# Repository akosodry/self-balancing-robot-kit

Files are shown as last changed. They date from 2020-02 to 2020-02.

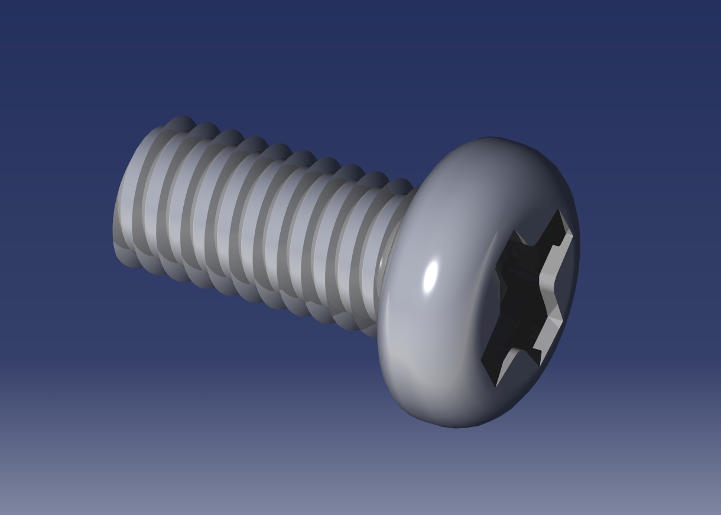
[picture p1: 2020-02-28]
2_Solidworks models (student work)/2_Solidworks models (student work)/m3x10-philips-head-screw-1.snapshot.2/M3x6.jpg

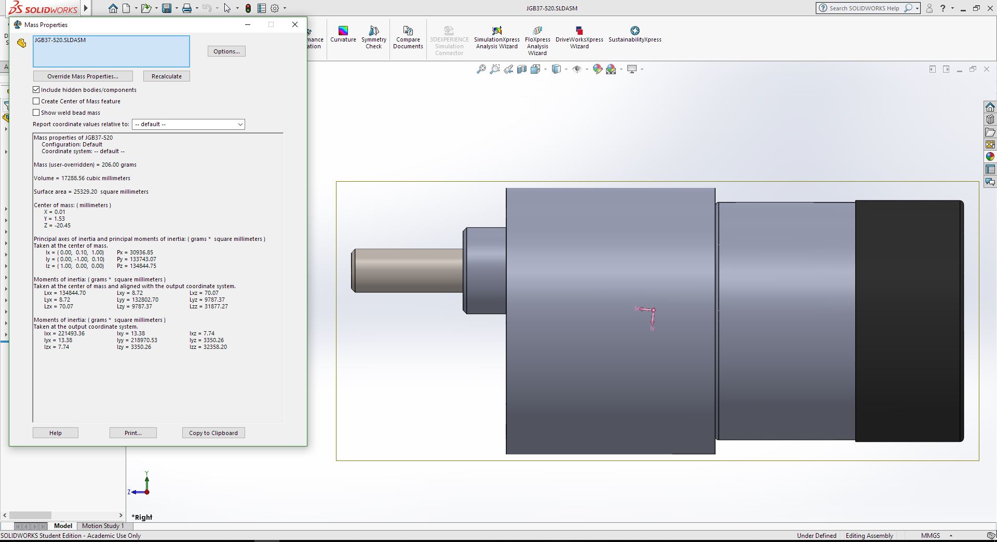
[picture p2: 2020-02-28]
2_Solidworks models (student work)/2_Solidworks models (student work)/Motor/Ellenőrző képek/Oldalnezet.JPG

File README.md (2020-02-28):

# self-balancing-robot-kit
The supplementary online material for the article: FUZZY CONTROL OF SELF‐BALANCING ROBOTS: A CONTROL LABORATORY PROJECT

**Cite this work as:**

Odry Á, Fullér R, Rudas IJ, Odry P. **Fuzzy control of self‐balancing robots: A control laboratory project**. Comput Appl Eng Educ. 2020;1–24. https://doi.org/10.1002/cae.22219

A **short video demonstration** of the closed loop behavior is available **here**:
https://youtu.be/y2i62vh2vE4

The paper systematically describes the construction, development and fuzzy control of the proposed lab setup for teaching control system design in laboratories. All the information, including the STL files for 3D printing, computer-aided design (CAD) models, MATLAB/Simulink files, and MCU software have been made publicly available here to help other lab teams in designing similar experiments.

The description of the files is summarized as follows.

**1_3D printer files** This file contains the STL files that can be used in 3D printing software such as Ultimaker Cura.

**2_Solidworks models** 	This file contains the CAD model of the lab setup. It was created by a mechatronic engineering student at the University of Dunaújváros.

**3_Minimal working environment**	This file contains the Arduino code that initializes the MCU peripherals of the lab setup, drives the motors in both directions, and reads and sends the instantaneous IMU (acceleration and angular rate) and encoder (motor shaft position) measurements to the PC.

**4_MATLAB script to record data**	This file contains the MATLAB code used to collect the measurement results via the serial port. The file also contains the recorded measurement results.

**5_DC motor model**	This file contains both the Simulink model of the DC motor and the Simulink Design Optimization session file.

**6_Robot model open loop**	This file contains the S-function-based Simulink model of the robot.

**7_Robot model closed loop**	This file contains the Simulink model of the fuzzy control strategy.

**8_LUT generation**	This file contains the MATLAB functions that generate the lookup-table approximation of the fuzzy logic controllers.

**9_Arduino closed loop**	This file contains the Arduino code that applies the fuzzy control strategy to stabilize the robot.

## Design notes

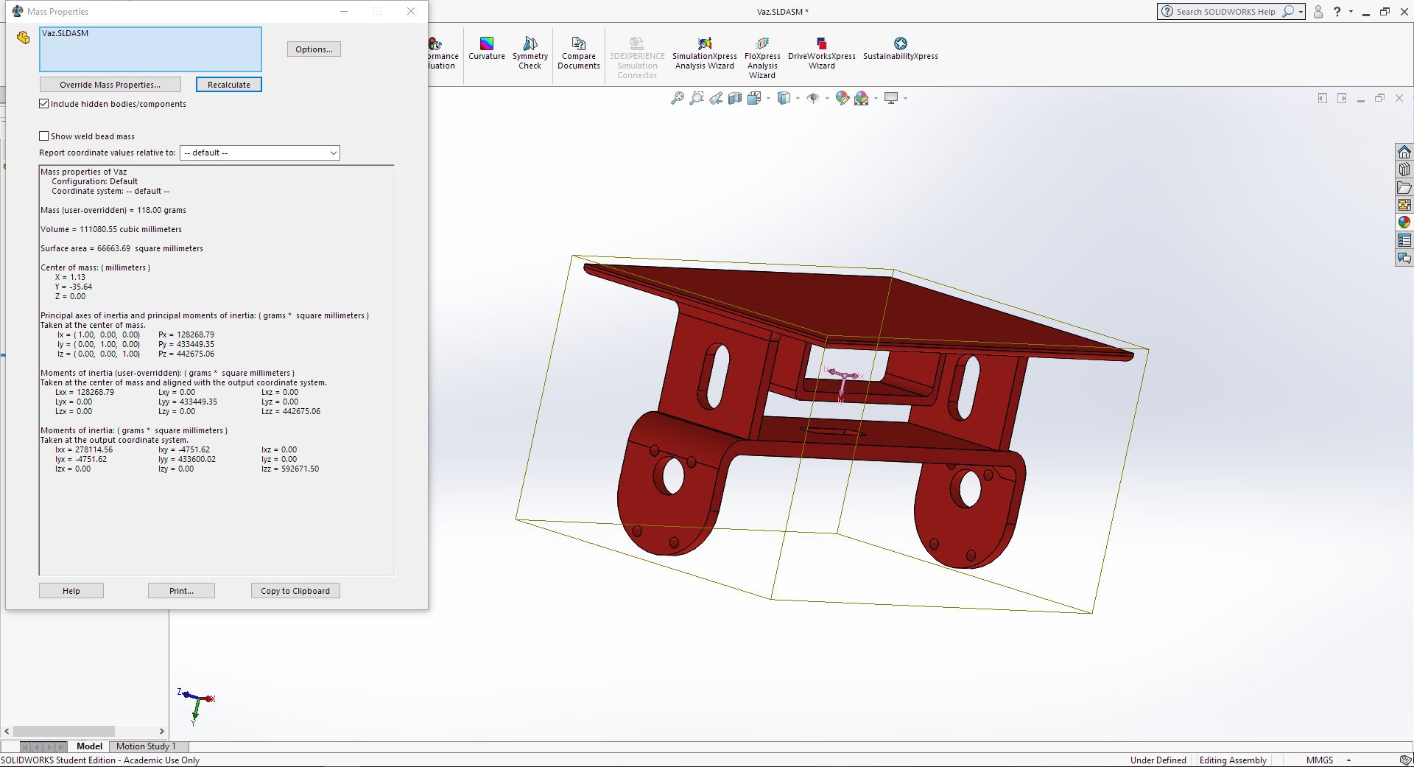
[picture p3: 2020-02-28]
2_Solidworks models (student work)/2_Solidworks models (student work)/Váz/Ellenőrző képek/Vaz_Ellenorzo.JPG

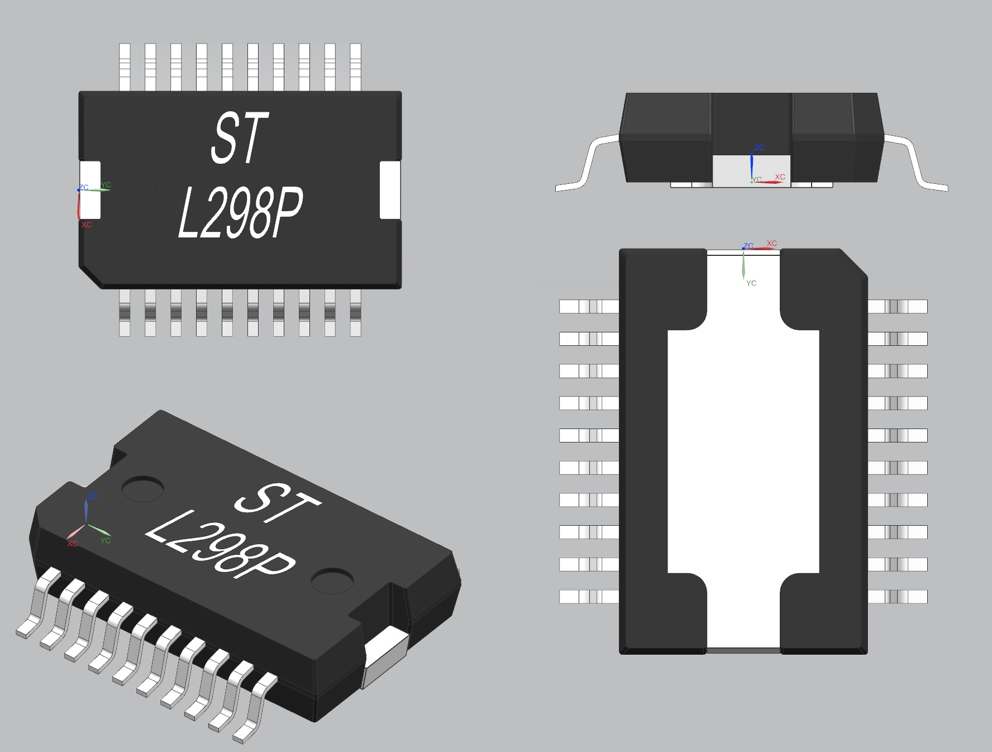
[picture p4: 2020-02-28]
2_Solidworks models (student work)/2_Solidworks models (student work)/H-híd/l298-l298p-1.snapshot.2/L298P.jpg

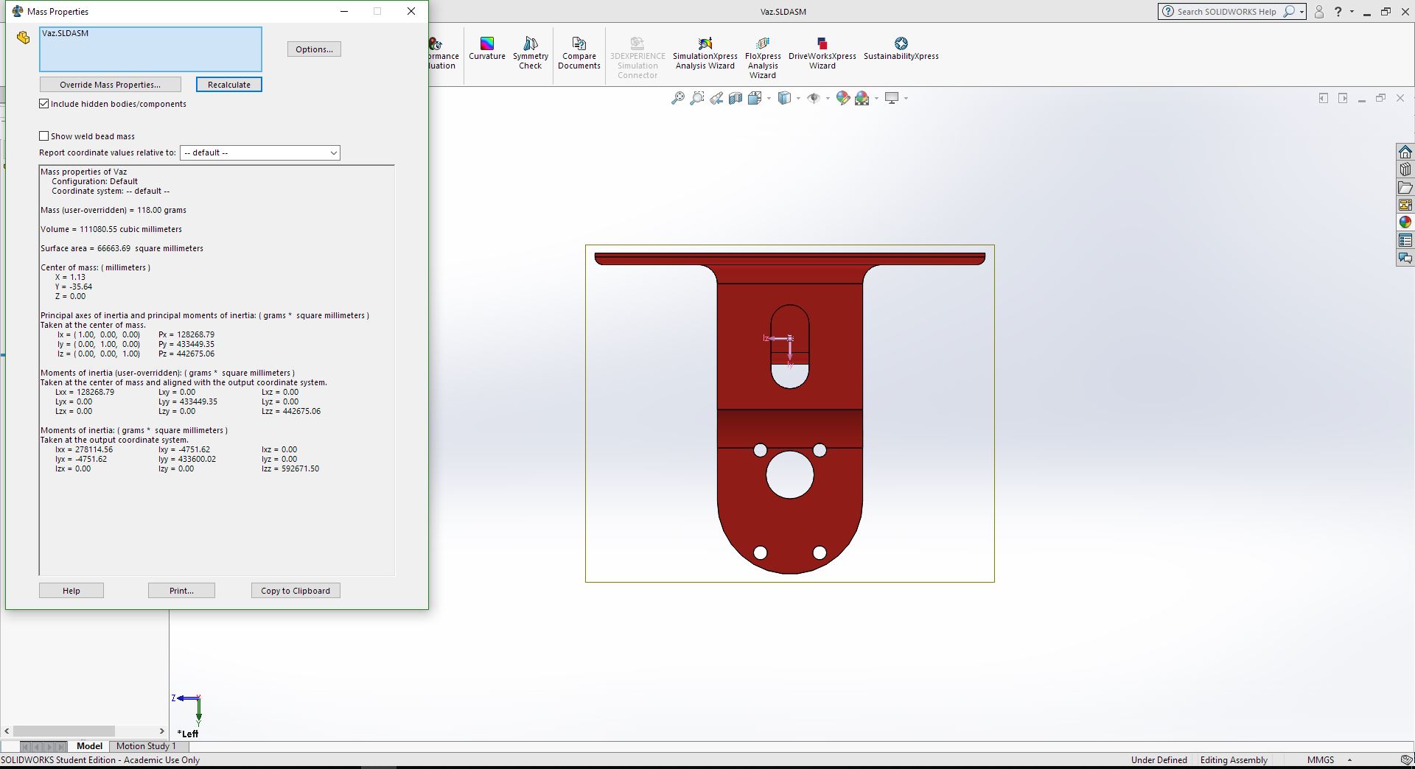
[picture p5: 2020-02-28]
2_Solidworks models (student work)/2_Solidworks models (student work)/Váz/Ellenőrző képek/Oldalnezet.JPG

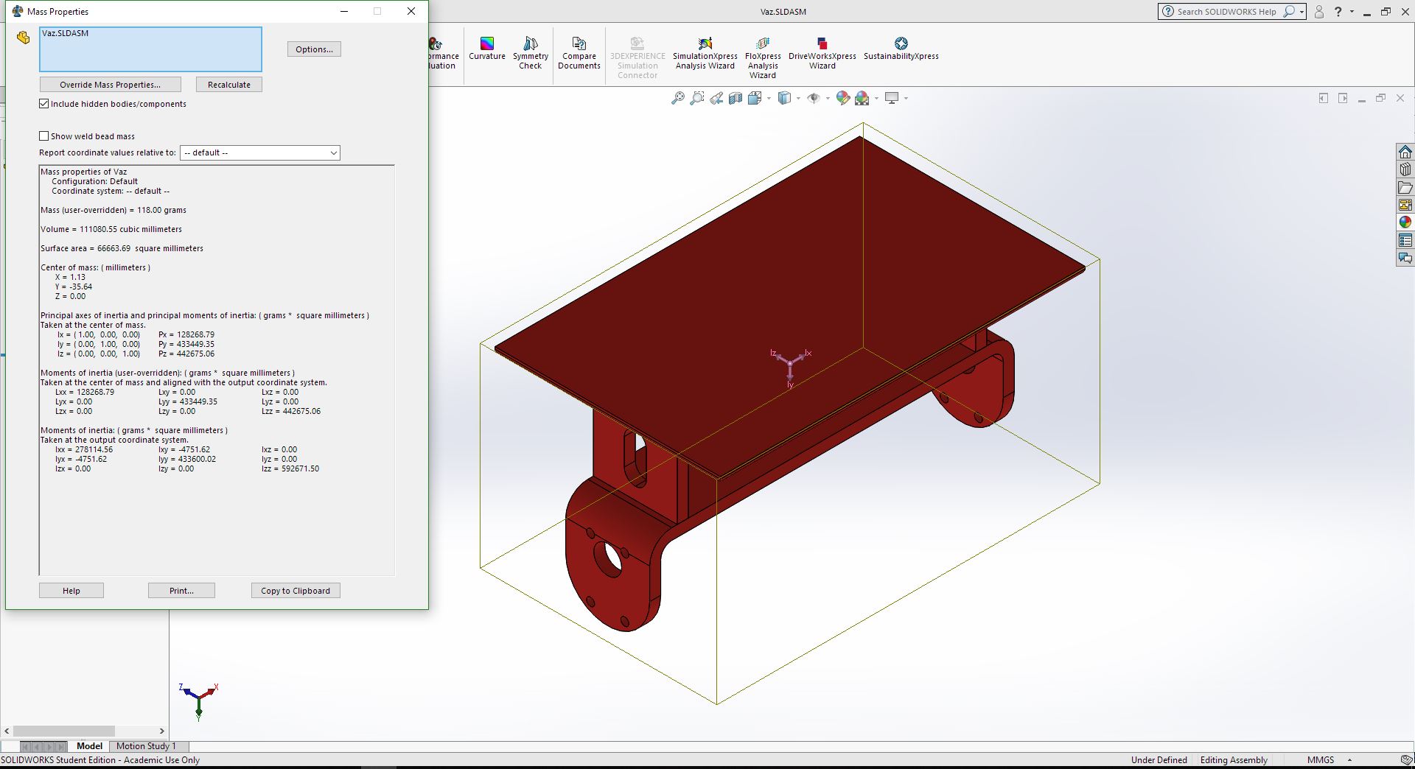
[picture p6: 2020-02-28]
2_Solidworks models (student work)/2_Solidworks models (student work)/Váz/Ellenőrző képek/axonometrikus.JPG

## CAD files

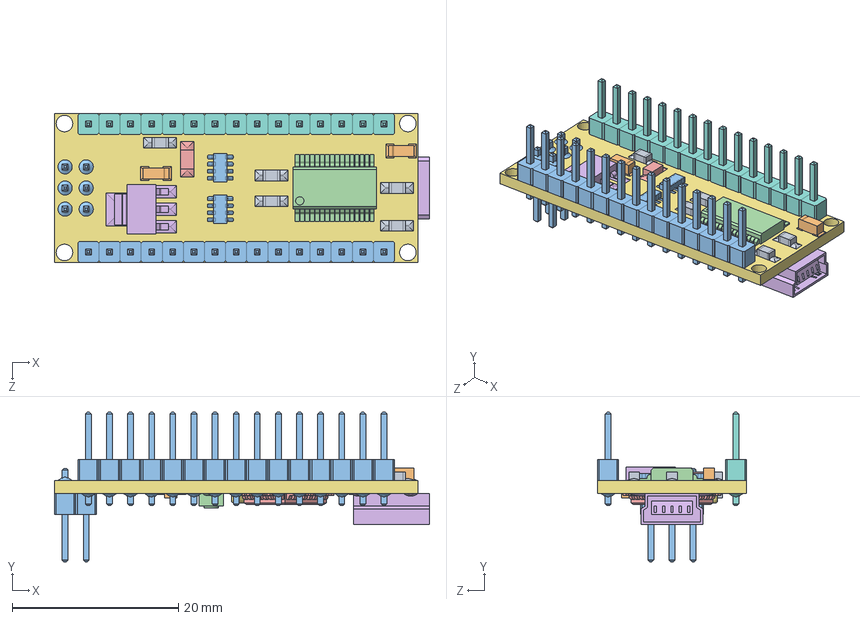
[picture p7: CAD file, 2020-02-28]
2_Solidworks models (student work)/2_Solidworks models (student work)/Arduino_NanoV3 v4/NanoV3 v4.SLDASM
45.1 x 18.0 x 17.9 mm
Led.step x 3
Led (1).step
Pin.step x 21
switch.step
chip1.step
USB.step
Crystal.step
Pin (1).step x 15
Res.step x 5
cap.step x 2
respack.step x 2
Chip.step
diode.step
vreg.step
PCB-0.step

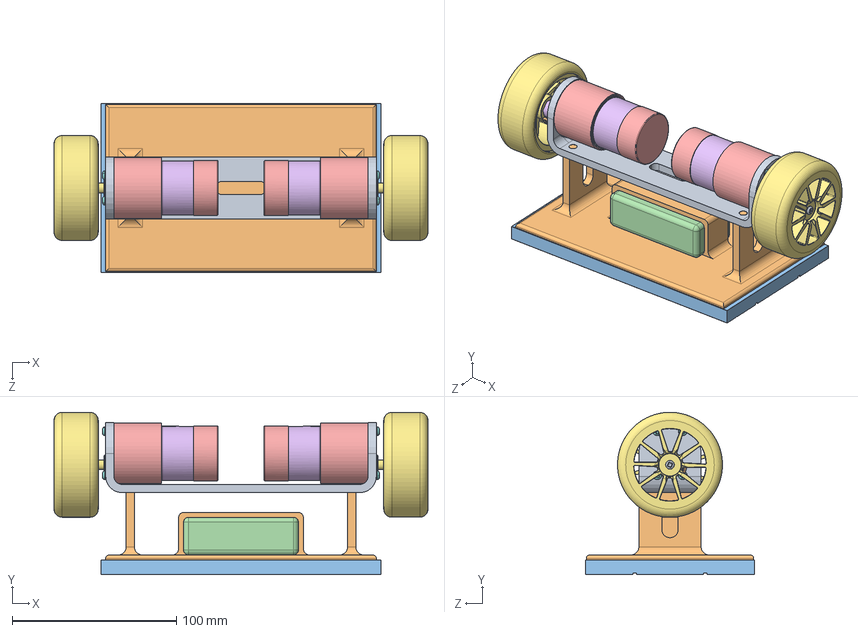
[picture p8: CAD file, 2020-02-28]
2_Solidworks models (student work)/2_Solidworks models (student work)/Osszeszereles.SLDASM
228.0 x 99.0 x 103.0 mm
base
table
Probapanel
Akksi
GEARED BODY, MOTOR, JGB37-520 x 2
DC MOTOR, JGB37-520 x 2
MOTOR SHAFT, JGB37-520 x 2
SHAFT COUPLER, JGB37-520 x 2
COUPLING BRACKET, GEARED BODY TO DC MOTOR, JGB37-520 x 2
PLASTIC COVER, DC MOTOR, JGB37-520 x 2
CONNECTION, DC MOTOR, JGB37-520 x 4
pan_head_phillip_mc_screw_m2 x 6
muanyag_fedo x 2
Felni_vivo_elem x 2
Kerek x 2
M3x10 Philips Screw x 8
M3x12 Philips Screw_part x 2
M3x6 Philips Screw_part x 2

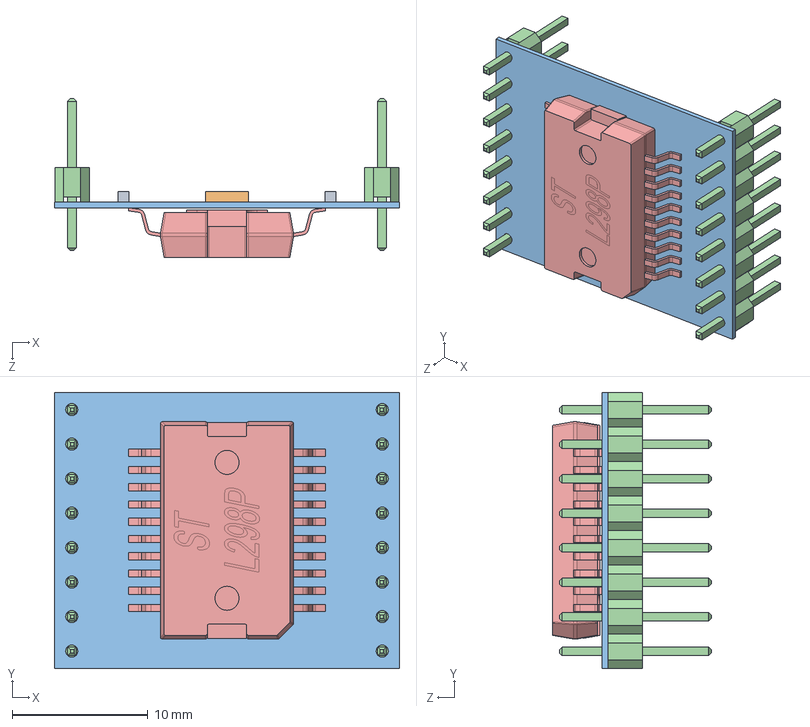
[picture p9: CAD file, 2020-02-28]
2_Solidworks models (student work)/2_Solidworks models (student work)/H-híd/H-BRIDGE_v2.SLDASM
25.4 x 20.3 x 11.7 mm
Extruded-0.step x 2
Extruded-1.step
Board.step
pin x 16
L298P

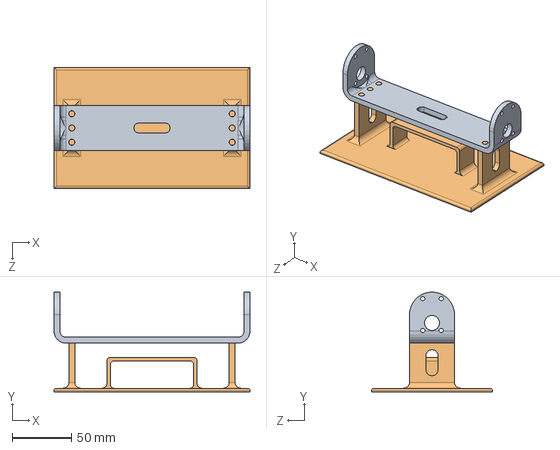
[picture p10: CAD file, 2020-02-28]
2_Solidworks models (student work)/2_Solidworks models (student work)/Váz/Vaz.SLDASM
165.0 x 83.9 x 102.0 mm
base
table

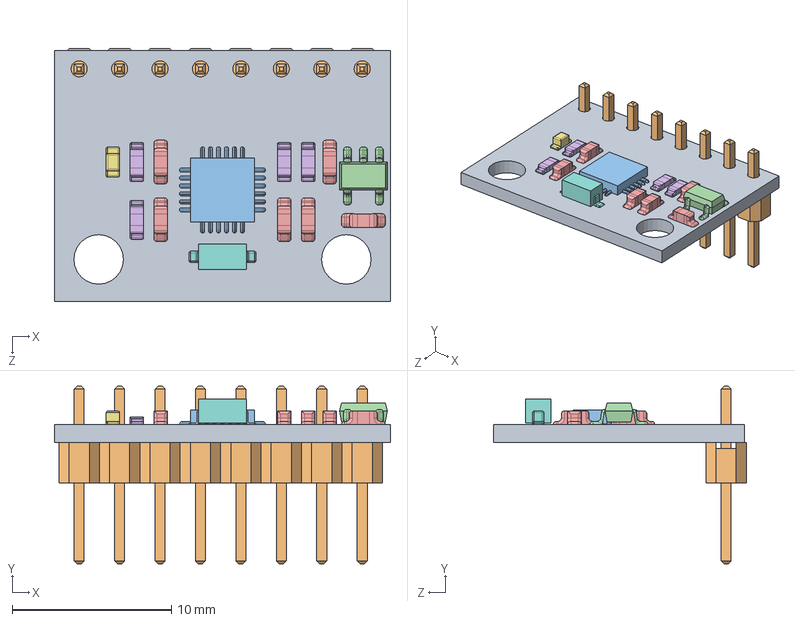
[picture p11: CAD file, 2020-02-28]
2_Solidworks models (student work)/2_Solidworks models (student work)/IMU_Szenzor/MPU 6050 IMU.SLDASM
21.1 x 11.2 x 15.9 mm
Base1
pin header x 8
sensor chip
S2NH chip
Resistor small x 6
Resistor small black x 4
Small LED
Resistor black

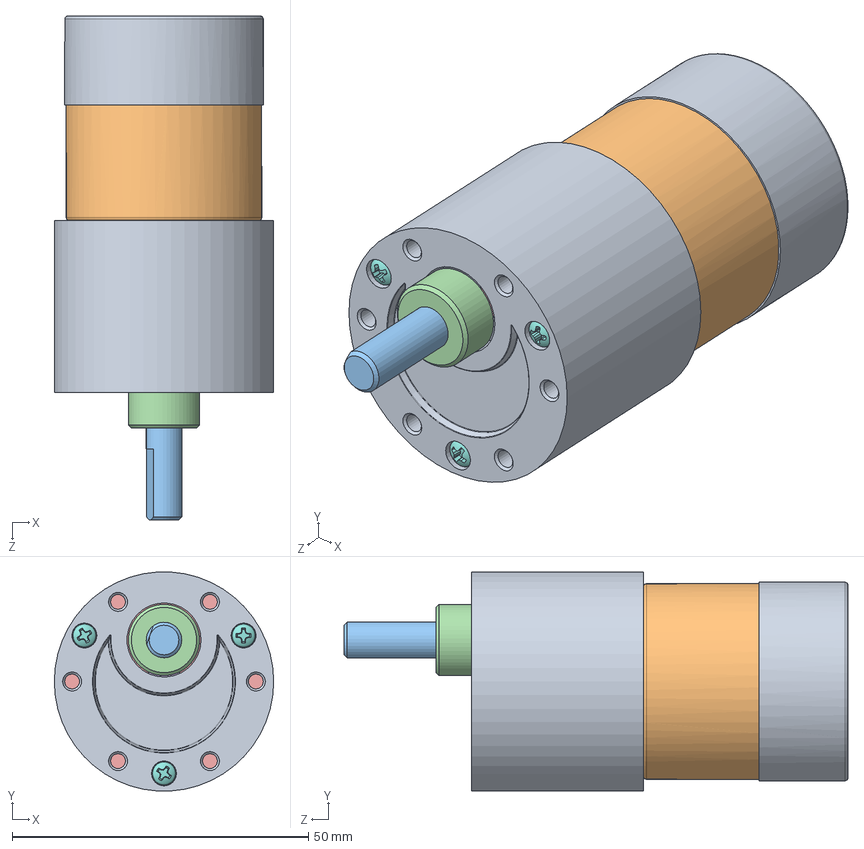
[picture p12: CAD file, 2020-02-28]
2_Solidworks models (student work)/2_Solidworks models (student work)/Motor/JGB37-520.SLDASM
37.0 x 36.9 x 85.0 mm
GEARED BODY, MOTOR, JGB37-520
DC MOTOR, JGB37-520
MOTOR SHAFT, JGB37-520
SHAFT COUPLER, JGB37-520
COUPLING BRACKET, GEARED BODY TO DC MOTOR, JGB37-520
PLASTIC COVER, DC MOTOR, JGB37-520
CONNECTION, DC MOTOR, JGB37-520 x 2
pan_head_phillip_mc_screw_m2 x 3
muanyag_fedo

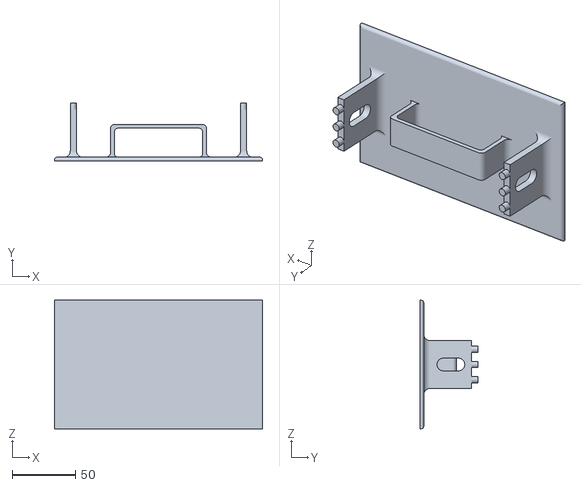
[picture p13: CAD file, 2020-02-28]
1_3D printer files/1_3D printer files/table.STL
165.0 x 46.0 x 102.0

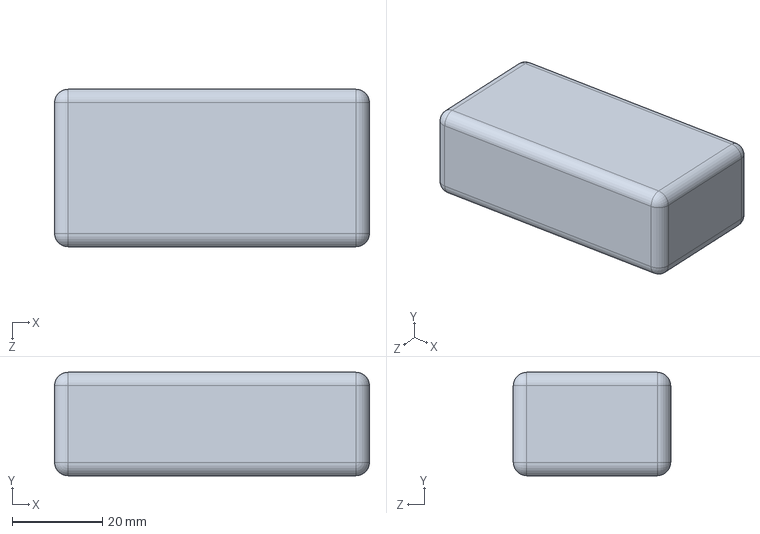
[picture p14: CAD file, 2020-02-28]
2_Solidworks models (student work)/2_Solidworks models (student work)/Akksi/Akksi.SLDPRT
70.0 x 23.0 x 35.0 mm

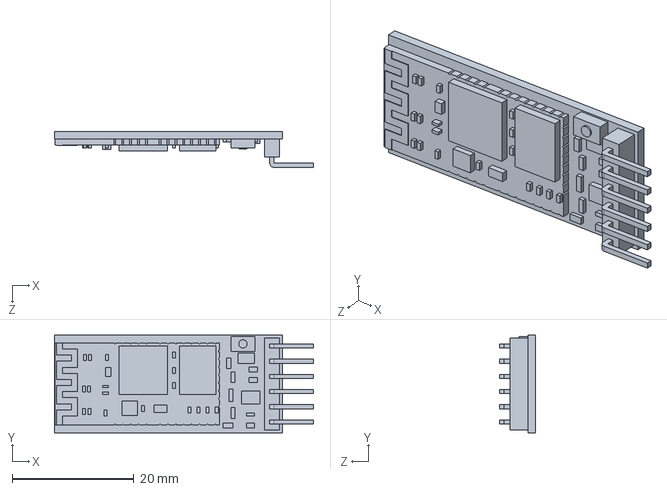
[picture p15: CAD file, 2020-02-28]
2_Solidworks models (student work)/2_Solidworks models (student work)/Bluetooth_modul/hc05.SLDPRT
42.6 x 16.1 x 5.90 mm

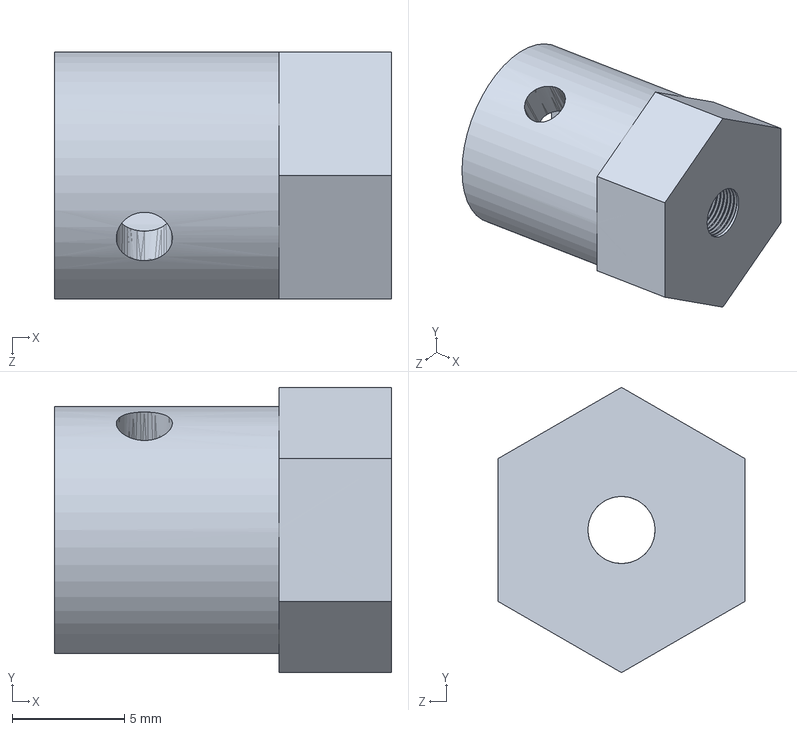
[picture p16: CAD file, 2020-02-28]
2_Solidworks models (student work)/2_Solidworks models (student work)/Felni vivő elem/Felni_vivo_elem.SLDPRT
15.0 x 12.7 x 11.0 mm

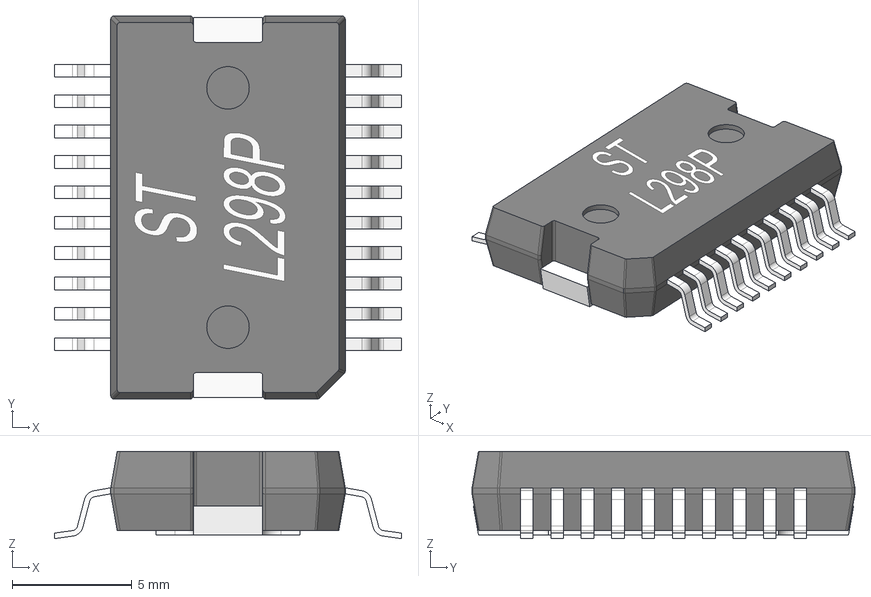
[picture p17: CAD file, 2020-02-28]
2_Solidworks models (student work)/2_Solidworks models (student work)/H-híd/l298-l298p-1.snapshot.2/L298_PowerSO20.stp
14.5 x 16.0 x 3.65 mm

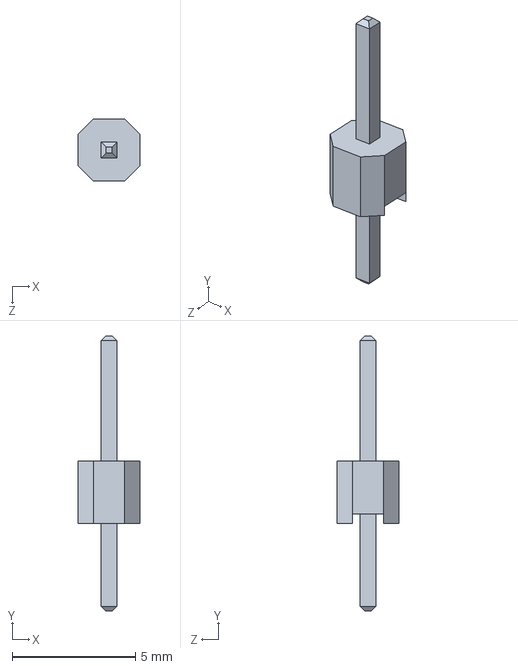
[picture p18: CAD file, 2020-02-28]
2_Solidworks models (student work)/2_Solidworks models (student work)/H-híd/pin.SLDPRT
2.54 x 11.2 x 2.54 mm

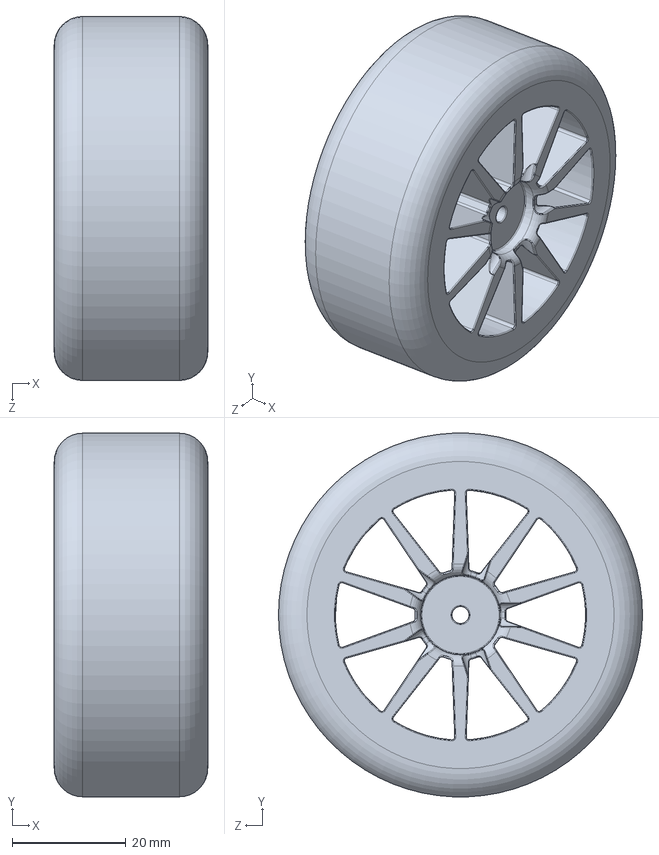
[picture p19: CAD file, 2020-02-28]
2_Solidworks models (student work)/2_Solidworks models (student work)/Kerék/Kerek.SLDPRT
27.0 x 63.9 x 64.0 mm

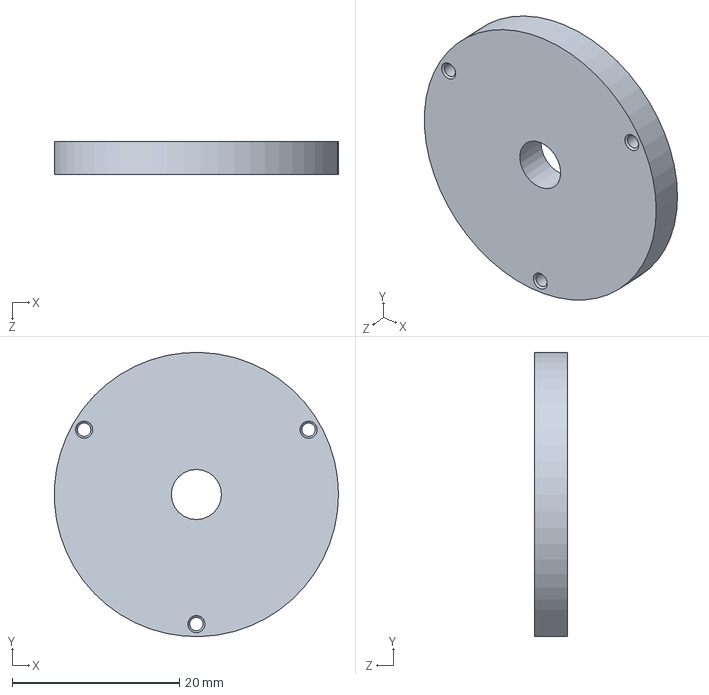
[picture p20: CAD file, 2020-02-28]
2_Solidworks models (student work)/2_Solidworks models (student work)/Motor/COUPLING BRACKET, GEARED BODY TO DC MOTOR, JGB37-520.SLDPRT
34.0 x 34.0 x 4.00 mm

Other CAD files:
2_Solidworks models (student work)/2_Solidworks models (student work)/IMU_Szenzor/pin header.SLDPRT
2_Solidworks models (student work)/2_Solidworks models (student work)/Váz/base.SLDPRT
2_Solidworks models (student work)/2_Solidworks models (student work)/IMU_Szenzor/Resistor small.SLDPRT
2_Solidworks models (student work)/2_Solidworks models (student work)/Váz/table.SLDPRT
2_Solidworks models (student work)/2_Solidworks models (student work)/H-híd/l298-l298p-1.snapshot.2/L298_PowerSO20.SLDPRT
2_Solidworks models (student work)/2_Solidworks models (student work)/IMU_Szenzor/Base.SLDPRT
2_Solidworks models (student work)/2_Solidworks models (student work)/IMU_Szenzor/Base1.SLDPRT
2_Solidworks models (student work)/2_Solidworks models (student work)/IMU_Szenzor/Resistor black.SLDPRT
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

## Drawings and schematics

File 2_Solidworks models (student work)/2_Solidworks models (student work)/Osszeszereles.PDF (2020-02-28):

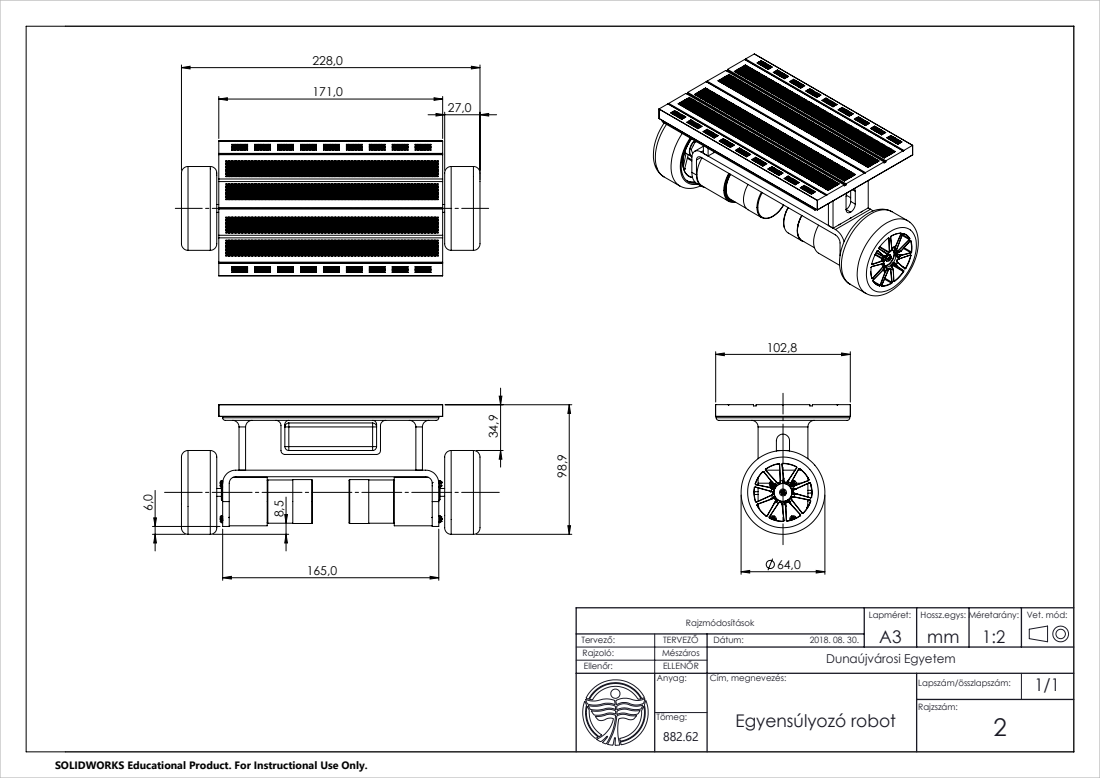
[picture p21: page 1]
2 Egyensúlyozó robot

Rajzmódosítások | Lapméret: A3 | Hossz.egys: Méretarány: | | Vet. mód:

Tervező: | | Dátum: 2018. 08. 30.
Rajzoló: | Mészáros | Dunaújvárosi Egyetem
Ellenőr: | ELLENŐR

Anyag: | Cím, megnevezés: | Lapszám/összlapszám: | 1/1

SOLIDWORKS Educational Product. For Instructional Use Only.

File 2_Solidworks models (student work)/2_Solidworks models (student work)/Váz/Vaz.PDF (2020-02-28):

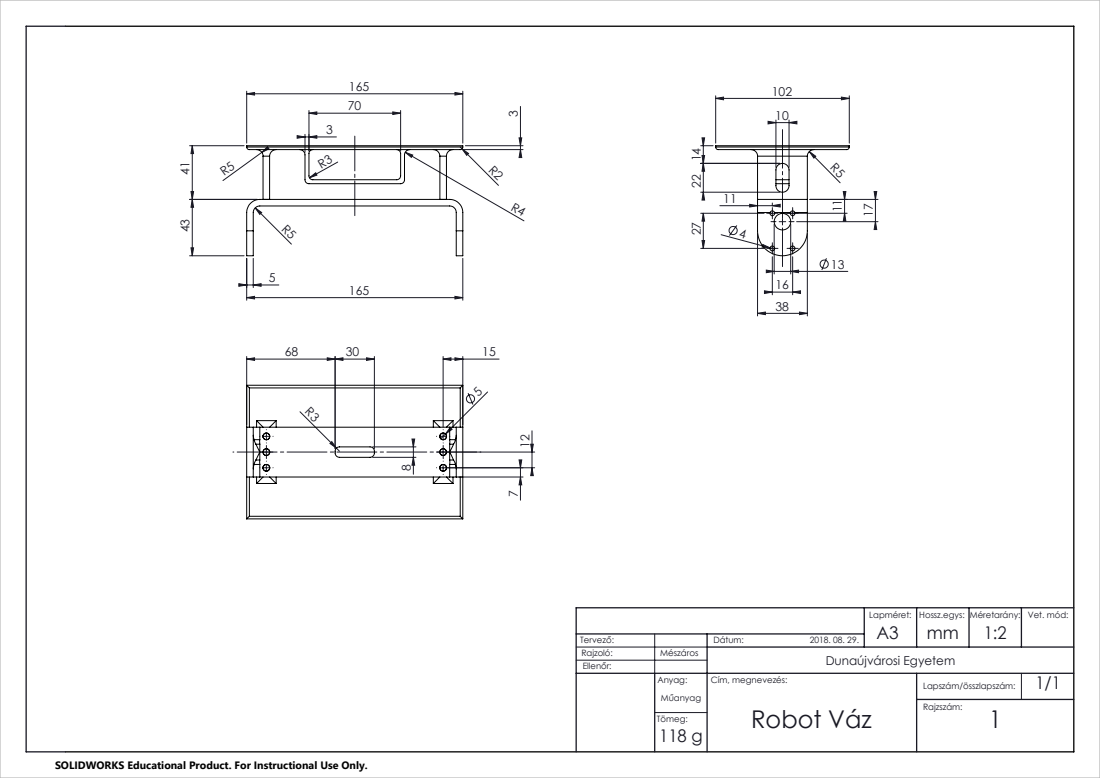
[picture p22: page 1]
Cím, megnevezés:; Robot Váz

2018. 08. 29. | Lapméret: A3 | Hossz.egys: mm | Méretarány: 1:2 | Vet. mód:

Tervező: | | Dátum:
Rajzoló: | Mészáros | Dunaújvárosi Egyetem
Ellenőr:

SOLIDWORKS Educational Product. For Instructional Use Only.

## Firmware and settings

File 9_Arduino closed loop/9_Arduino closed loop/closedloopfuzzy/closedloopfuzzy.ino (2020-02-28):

#include <avr/pgmspace.h>
#include <Wire.h>
#include <digitalWriteFast.h>
#include <PWM.h>
#include "FLC1.h"
#include "FLC2.h"
#include "FLC3.h"

// IMU
#define MPU_ADDR 0x68
#define SMPRT_DIV 0x19
#define CONFIG_REG 0x20
#define PWR_MGMT_1 0x6B
#define GYRO_CONFIG 0x1B
#define ACCEL_CONFIG 0x1C

#define ACCEL_XOUT_H 0x3B
#define GYRO_XOUT_H 0x43

#define IMU_READ_SUCCESS   0
#define I2C_TIMEOUT_ERROR  5
#define I2C_TIMEOUT        1000
#define I2C_DATA_NO        14
uint8_t i2cData[I2C_DATA_NO];

#define CALIB_DATA_NO 50
float tempData = 0;

int16_t accelX, accelY, accelZ;
int16_t gyroX, gyroY, gyroZ;
float angle, rate;
float estAngle = 0;

float angle_offs = -0.388;
float rate_offs = -0.03;

#define ANGLE_ATAN

// H-BRIDGE, MOTOR+ENC
#define PWMFREQ 10000

#define MOT1_CHA 4
#define MOT1_CHB 2
#define IN1 11
#define IN2 12
#define ENA 10

#define MOT2_CHA 3
#define MOT2_CHB 5
#define IN3 8
#define IN4 7
#define ENB 9

int mot1Pos = 0;
int mot2Pos = 0;
int mot1Pwm;
int mot2Pwm;

// DUMMY
uint32_t timerXms;
uint32_t timerXs;
uint32_t timerXs2;

int vel1;
int vel2;
int vel;
int pos1 = 0;
int pos2 = 0;
int pos = 0;
int yaw = 0;
int desPos = 0;
int desYaw = 0;

int angleControlPWM = 0;
int yawControlPWM = 0;

//#define CALIB_GYRO
#define DEAD_BAND
#define DEAD_BAND_PWMVAL 110
//#define DESVALS
int desValStates = 0;

int conseqTimeOutCntr = 0;

#define SEND_TO_PC

void setup()
{
  InitTimersSafe();  
  SetPinFrequencySafe(ENA, PWMFREQ);
  SetPinFrequencySafe(ENB, PWMFREQ);

  Serial.begin(9600);

  // IMU
  Wire.begin();
  Wire.setClock(400000UL); 
  Wire.beginTransmission(MPU_ADDR);
  Wire.write(PWR_MGMT_1);
  Wire.write(0b00000000); // deactivate sleep mode
  Wire.endTransmission();

  delay(100);

  Wire.beginTransmission(MPU_ADDR);
  Wire.write(SMPRT_DIV);
  Wire.write(0b00000100); // sampling 200Hz
  Wire.endTransmission();

  delay(100);

  Wire.beginTransmission(MPU_ADDR);
  Wire.write(CONFIG_REG);
  Wire.write(0x03);       // Accel 44 Hz cut, Gyro 42 Hz cut, 1000 Hz sampling
  Wire.endTransmission();

  delay(100);

  Wire.beginTransmission(MPU_ADDR);
  Wire.write(GYRO_CONFIG);
  Wire.write(0x00000000); // 250 dps
  Wire.endTransmission();

  delay(100);

  Wire.beginTransmission(MPU_ADDR);
  Wire.write(ACCEL_CONFIG);
  Wire.write(0b00000000); // 2 g
  Wire.endTransmission();

  // H-BRIDGE, MOTOR+ENC
  pinMode(IN1, OUTPUT);
  pinMode(IN2, OUTPUT);
  //pinMode(ENA, OUTPUT);
  //digitalWriteFast(ENA, LOW);
  pwmWrite(ENA, 0);

  pinMode(IN3, OUTPUT);
  pinMode(IN4, OUTPUT);
  //pinMode(ENB, OUTPUT);
  //digitalWriteFast(ENA, LOW);
  pwmWrite(ENB, 0);

  pinMode(MOT1_CHA, INPUT);
  pinMode(MOT1_CHB, INPUT);
  pinMode(MOT2_CHA, INPUT);
  pinMode(MOT2_CHB, INPUT);

  attachInterrupt(digitalPinToInterrupt(MOT1_CHB), MOT1_CHB_FALL, FALLING);
  attachInterrupt(digitalPinToInterrupt(MOT2_CHA), MOT2_CHA_FALL, FALLING);

#ifdef CALIB_GYRO
  for (int i = 0; i < CALIB_DATA_NO; i++)
  {
    getImuData();
    tempData = tempData + rate;
  }

  rate_offs = tempData / CALIB_DATA_NO;
  Serial.println(rate_offs);
#endif

  pinMode(LED_BUILTIN, OUTPUT);

  delay(3000);  
}

void loop()
{
  //10ms
  if ((micros() - timerXms) >= 10000)
  {
    timerXms = micros();

    vel1 = mot1Pos;         // inc/10ms
    vel2 = mot2Pos;         // inc/10ms
    mot1Pos = 0;
    mot2Pos = 0;

    if(getImuData() == IMU_READ_SUCCESS)
    {
      estAngle = 0.99f * (estAngle + rate * 0.01f) + 0.01f * angle;
      conseqTimeOutCntr = 0;
    }
    else
    {
      conseqTimeOutCntr++;
      if (conseqTimeOutCntr > 50)
      {
        errorHandling();     
      }
    }

    pos1 = pos1 + vel1;
    pos2 = pos2 + vel2;
    pos = (pos1+pos2)>>1;
    vel = (vel1+vel2)>>1;
    yaw = pos2-pos1;
    
    #if 1
    if ((estAngle > -45) && (estAngle < 45))
    {
      angleControlPWM = FLC((0-estAngle), (0-rate), in1min_FLC2, in2min_FLC2, res1_FLC2, res2_FLC2, *FLC2, NROW_FLC2, NCOL_FLC2) - FLC(((float)(desPos-pos)), ((float)(0-vel)), in1min_FLC1, in2min_FLC1, res1_FLC1, res2_FLC1, *FLC1, NROW_FLC1, NCOL_FLC1);
      yawControlPWM = -FLC(((float)(desYaw-yaw)), ((float)(0-(vel2-vel1))), in1min_FLC3, in2min_FLC3, res1_FLC3, res2_FLC3, *FLC3, NROW_FLC3, NCOL_FLC3);
      
      #ifdef DEAD_BAND
        if (angleControlPWM > 0)
        {
          setMot1Pwm(angleControlPWM+yawControlPWM + DEAD_BAND_PWMVAL);
          setMot2Pwm(angleControlPWM-yawControlPWM + DEAD_BAND_PWMVAL);
        }
        else
        {
          setMot1Pwm(angleControlPWM+yawControlPWM - DEAD_BAND_PWMVAL);
          setMot2Pwm(angleControlPWM-yawControlPWM - DEAD_BAND_PWMVAL);
        }
      #else
        setMot1Pwm(angleControlPWM);
        setMot2Pwm(angleControlPWM);
      #endif
    }
    else
    {
      pos1 = 0;
      pos2 = 0;
      vel1 = 0;
      vel2 = 0;
      mot1Pos = 0;
      mot2Pos = 0;
      pos = 0;
      vel = 0;
      stopMotors();
    }
    #endif
  }

  #ifdef DESVALS // 4sec
  if(((millis() - timerXs) >= 4000))
  {
    timerXs = millis();

    if(desValStates == 0)
    {
      desPos = 592;
      desValStates = 1;
    }
    else if(desValStates == 1)
    {
      //desPos = 0;
      desYaw = 748;
      desValStates = 2;
    }
    else if(desValStates == 2)
    {
      desPos = 100;
      desValStates = 3;
    }
    else if(desValStates == 3)
    {
      desYaw = -200;
      desValStates = 4;
    }
    else if(desValStates == 4)
    {
      desPos = -400;
      desValStates = 5;
    }
    else if(desValStates == 5)
    {
      desPos = 0;
      desYaw = 0;
      desValStates = 0;
    }
  }  
  #endif

  #ifdef SEND_TO_PC // 40ms
  if(((millis() - timerXs2) >= 50))
  {
    timerXs2 = millis();
  
    Serial.print(desPos);
    Serial.print(',');
    Serial.print(pos);
    Serial.print(',');
    Serial.print(desYaw);
    Serial.print(',');
    Serial.print(yaw);
    Serial.print(',');
    Serial.print(angle);
    Serial.print(',');
    Serial.print(estAngle);
    Serial.print(',');
    Serial.print(mot1Pwm);
    Serial.print(',');
    Serial.println(mot2Pwm);
  }
  #endif
}

void errorHandling()
{
  while (1)      
  {
    stopMotors();
    stopMotors();
        
    digitalWriteFast(LED_BUILTIN, HIGH);   
    delay(500);                            
    digitalWriteFast(LED_BUILTIN, LOW);    
    delay(500);
   }
}

uint8_t getImuData()
{
  uint32_t i2cTimeOutTimer;

  Wire.beginTransmission(MPU_ADDR);
  Wire.write(ACCEL_XOUT_H);

  uint8_t i2cReturnCode = Wire.endTransmission(false);
  if (i2cReturnCode)
  {
    return i2cReturnCode;
  }

  Wire.requestFrom(MPU_ADDR, I2C_DATA_NO, (uint8_t)true);

  for (uint8_t i = 0; i < I2C_DATA_NO; i++)
  {
    if (Wire.available())
    {
      i2cData[i] = Wire.read();
    }
    else
    {
      i2cTimeOutTimer = micros();
      while (((micros() - i2cTimeOutTimer) < I2C_TIMEOUT) && !Wire.available());
      if (Wire.available())
      {
        i2cData[i] = Wire.read();
      }
      else
      {
        return I2C_TIMEOUT_ERROR;
      }
    }
  }

  accelX = ((i2cData[0] << 8) | i2cData[1]);
  //accelY = ((i2cData[2] << 8) | i2cData[3]);
  accelZ = ((i2cData[4] << 8) | i2cData[5]);
  //int16_t tempOut = ((i2cData[6] << 8) | i2cData[7]);
  //gyroX = ((i2cData[8] << 8) | i2cData[9]);
  gyroY = ((i2cData[10] << 8) | i2cData[11]);
  //gyroZ = ((i2cData[12] << 8) | i2cData[13]);

#ifdef ANGLE_ATAN
  angle = atan2((float)accelX, (float)accelZ) * RAD_TO_DEG;
#else
  angle = ((float)accelX) / 16384.0f;
#endif
  angle = angle - angle_offs;

  rate = -((float)gyroY) / 131.0f;
  rate = rate - rate_offs;

  return IMU_READ_SUCCESS;
}

void stopMotors()
{
  digitalWriteFast(IN1, LOW);
  digitalWriteFast(IN2, LOW);
  pwmWrite(ENA, 0);

  digitalWriteFast(IN3, LOW);
  digitalWriteFast(IN4, LOW);
  pwmWrite(ENB, 0);
}

void setMot1Pwm(int pwmVal)
{
  if (pwmVal > 255)
    pwmVal = 255;
  else if (pwmVal < -255)
    pwmVal = -255;

  if (pwmVal > 0)						//forward
  {
    //digitalWriteFast(ENA, LOW);
    digitalWriteFast(IN1, LOW);
    digitalWriteFast(IN2, HIGH);
    //analogWrite(ENA, pwmVal);
    pwmWrite(ENA, pwmVal);
  }
  else								//backward
  {
    //digitalWriteFast(ENA, LOW);
    digitalWriteFast(IN1, HIGH);
    digitalWriteFast(IN2, LOW);
    //analogWrite(ENA, -pwmVal);
    pwmWrite(ENA, -pwmVal);
  }

  mot1Pwm = pwmVal;
}

void setMot2Pwm(int pwmVal)
{
  if (pwmVal > 255)
    pwmVal = 255;
  else if (pwmVal < -255)
    pwmVal = -255;

  if (pwmVal > 0)						//forward
  {
    //digitalWriteFast(ENB, LOW);
    digitalWriteFast(IN3, HIGH);
    digitalWriteFast(IN4, LOW);
    //analogWrite(ENB, pwmVal);
    pwmWrite(ENB, pwmVal);
  }
  else								      //backward
  {
    //digitalWriteFast(ENB, LOW);
    digitalWriteFast(IN3, LOW);
    digitalWriteFast(IN4, HIGH);
    //analogWrite(ENB, -pwmVal);
    pwmWrite(ENB, -pwmVal);
  }

  mot2Pwm = pwmVal;
}


void MOT1_CHB_FALL()
{
  if (digitalRead(MOT1_CHA) == HIGH)
    mot1Pos++;
  else
    mot1Pos--;
}

void MOT2_CHA_FALL()
{
  if (digitalRead(MOT2_CHB) == HIGH)
    mot2Pos++;
  else
    mot2Pos--;
}


int FLC(float e, float de, float in1min, float in2min, float res1, float res2, const int16_t* LUT, int rows, int cols)
{
  // saturation
  if(e<in1min)  e = in1min;
  if(de<in2min) de = in2min;
  
  // row and column indexes
  int ind1 = round((e-in1min)/res1); 
  int ind2 = round((de-in2min)/res2);
  
  // saturation
  if(ind1>rows-1) ind1 = rows-1;
  if(ind2>cols-1) ind2 = cols-1;
  
  return pgm_read_word_near(&LUT[ind1*cols+ind2]);
}

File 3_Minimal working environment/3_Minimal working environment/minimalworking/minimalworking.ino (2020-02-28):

#define MOT1_CHA 4
#define MOT1_CHB 2
#define IN1 11
#define IN2 12
#define ENA 10

#define MOT2_CHA 3
#define MOT2_CHB 5
#define IN3 8
#define IN4 7
#define ENB 9

#define DECODE1X

int mot1Pos = 0;
int mot2Pos = 0;
int mot1Pwm;
int mot2Pwm;

uint32_t timerXms;
uint32_t timerXs;
uint32_t timerXs2;

int tmpVal1;
int tmpVal2;

int flag = 0;
int flag2 = 1;

uint8_t increment = 0;

void setup() 
{
  Serial.begin(115200);
  pinMode(IN1, OUTPUT);
  pinMode(IN2, OUTPUT);
  pinMode(ENA, OUTPUT);
  digitalWrite(ENA, LOW);
  
  pinMode(IN3, OUTPUT);
  pinMode(IN4, OUTPUT);
  pinMode(ENB, OUTPUT);
  digitalWrite(ENB, LOW);

  pinMode(MOT1_CHA, INPUT);
  pinMode(MOT1_CHB, INPUT);
  pinMode(MOT2_CHA, INPUT);
  pinMode(MOT2_CHB, INPUT);

  #ifdef DECODE1X
    attachInterrupt(digitalPinToInterrupt(MOT1_CHB), MOT1_CHB_FALL, FALLING);
    attachInterrupt(digitalPinToInterrupt(MOT2_CHA), MOT2_CHA_FALL, FALLING);
  #else
    attachInterrupt(digitalPinToInterrupt(MOT1_CHB), MOT1_CHB_CHANGE, CHANGE);
    attachInterrupt(digitalPinToInterrupt(MOT2_CHA), MOT2_CHA_CHANGE, CHANGE);
  #endif
}

void loop() 
{
  //20ms
  if((micros() - timerXms) >= 20000) 
  {
    tmpVal1 = mot1Pos;
	tmpVal2 = mot2Pos;
    mot1Pos = 0;
	mot2Pos = 0;
    
    timerXms = micros();
    
    Serial.print(mot1Pwm);
    Serial.print(',');
    Serial.print(tmpVal1);
    Serial.print(',');
    Serial.print(mot2Pwm);
    Serial.print(',');
    Serial.println(tmpVal2);
  }

  //2sec
  if(((millis() - timerXs) >= 2000))
  {
    timerXs = millis();

    setMot1Pwm(150*flag);
	setMot2Pwm(150*flag);

    if(flag == 1)
      flag = -1;
    else if(flag == -1)
      flag = 0;
    else if(flag == 0)
      flag = 1;
  }

}

void setMot1Pwm(int pwmVal)
{
	if(pwmVal>255)
		pwmVal = 255;
	else if(pwmVal<-255)
		pwmVal = -255;
	
	if(pwmVal > 0)						//forward
	{
		digitalWrite(ENA, LOW);
		digitalWrite(IN1, LOW);
		digitalWrite(IN2, HIGH);
		analogWrite(ENA, pwmVal);
	}
	else								//backward
	{
		digitalWrite(ENA, LOW);
		digitalWrite(IN1, HIGH);
		digitalWrite(IN2, LOW);
		analogWrite(ENA, -pwmVal);	
	}
	
	mot1Pwm = pwmVal;
}

void setMot2Pwm(int pwmVal)
{
	if(pwmVal>255)
		pwmVal = 255;
	else if(pwmVal<-255)
		pwmVal = -255;
	
	if(pwmVal > 0)						//forward
	{
		digitalWrite(ENB, LOW);
		digitalWrite(IN3, HIGH);
		digitalWrite(IN4, LOW);
		analogWrite(ENB, pwmVal);
	}
	else								//backward
	{
		digitalWrite(ENB, LOW);
		digitalWrite(IN3, LOW);
		digitalWrite(IN4, HIGH);
		analogWrite(ENB, -pwmVal);	
	}
	
	mot2Pwm = pwmVal;
}

#ifdef DECODE1X
  void MOT1_CHB_FALL()
  {
    if(digitalRead(MOT1_CHA) == HIGH)
      mot1Pos++;
    else
      mot1Pos--;
  }

  void MOT2_CHA_FALL()
  {
    if(digitalRead(MOT2_CHB) == HIGH)
      mot2Pos++;
    else
      mot2Pos--;
  }
#else
  void MOT1_CHB_CHANGE()
  {
    if(digitalRead(MOT1_CHA) == HIGH)
    {
      if(digitalRead(MOT1_CHB) == LOW)
        mot1Pos++;
      else
        mot1Pos--;
    }
    else
    {
      if(digitalRead(MOT1_CHB) == LOW)
        mot1Pos--;
      else
        mot1Pos++;   
    } 
  }
#endif
